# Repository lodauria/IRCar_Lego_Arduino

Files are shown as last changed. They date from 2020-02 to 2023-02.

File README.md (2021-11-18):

# Lego car controlled with IR
As optional project for the Reti Logiche course me and [Giorgia Benci](https://www.linkedin.com/in/giorgia-benci-1a4912186/) have created with Legos a remote controlled car that uses an Arduino Uno on board to control the electronic components, in particular a DC motor, a servomotor and a IR receiver. The remote control is performed using a Wii Nunchuk connected to an Arduino Uno that communicates with the car through an infrared LED. The main feature is that to control the car it can be used ether the joystick or the accelerometers of the Wii Nunchuk. 

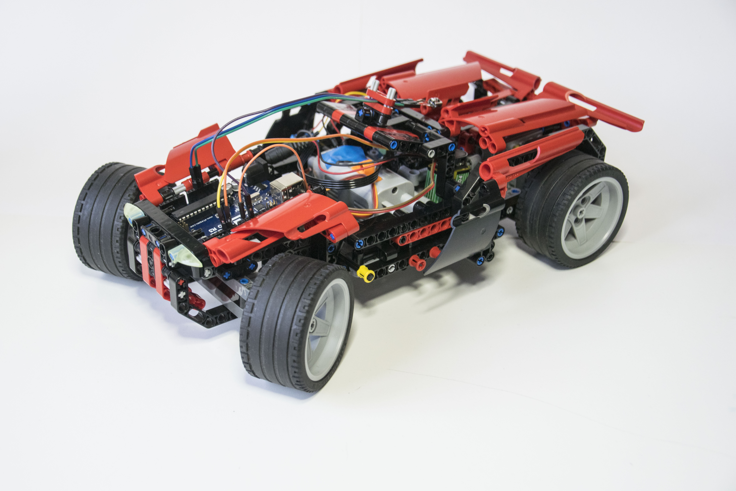
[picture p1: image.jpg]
Lego car


The Lego instructions are available [here](./LDD_files/Instructions), while the Lego Digital Designer 3D models can be found [here](./LDD_files/Models). The Arduino software developed is organized in the dedicated folders: [remote](./IRremote), [car](/IRlegocar).

***For Italian users*:** the complete documentation can be found [here](./Documentation.pdf).

## Demo video

To see the prototype in action and for more details about the system configuration watch the [video tutorial](https://youtu.be/qfQm9lA7alI).

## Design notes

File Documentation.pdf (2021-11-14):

# Macchina LEGO comandata a distanza

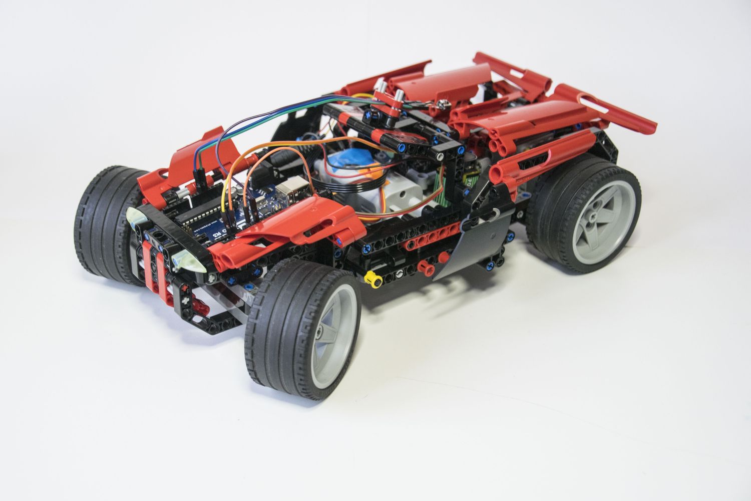
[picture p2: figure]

A cura di D’Auria Lorenzo e Benci Giorgia

## Introduzione

Il progetto in questione consiste nel comandare a distanza un’automobile costruita con i pezzi LEGO facendo uso del Nunchuk (controller di movimento) della Nintendo. Ciò avviene tramite la comunicazione infrarossi tra l’Arduino collegato al Nunchuk e l’Arduino integrato nella macchina LEGO. Come supporto alle componenti elettroniche, la scelta è ricaduta sui pezzi LEGO in quanto facilmente reperibili e maneggiabili.

## Descrizione della macchina

L’automobile è stata progettata in modo tale da ospitare in maniera specifica l’elettronica utilizzata, sfruttando inoltre il motore DC e la batteria in dotazione con i kit della LEGO (video dettagliato sull’adattamento di queste componenti). (https://youtu.be/au9P1RdKljY) Viene utilizzato un servo motore (anche esso adattato ai pezzi lego) (https://youtu.be/GeBPa39FLWI) per far sterzare le ruote anteriori, mentre il motore DC provvede da solo alla trazione attraverso le ruote posteriori. Per ottimizzarne le prestazioni del motore LEGO è stato necessario modificare la velocità di rotazione delle ruote attraverso una specifica combinazione di ingranaggi. Con l’ausilio del programma LEGO Digital Designer sono state generate le istruzioni dettagliate per la ricostruzione di questo modello (Istruzioni in PDF e modello 3D). (https://1drv.ms/f/s!AjiY4rjAO0lFgdFoaBNETIV-_LNzZQ)

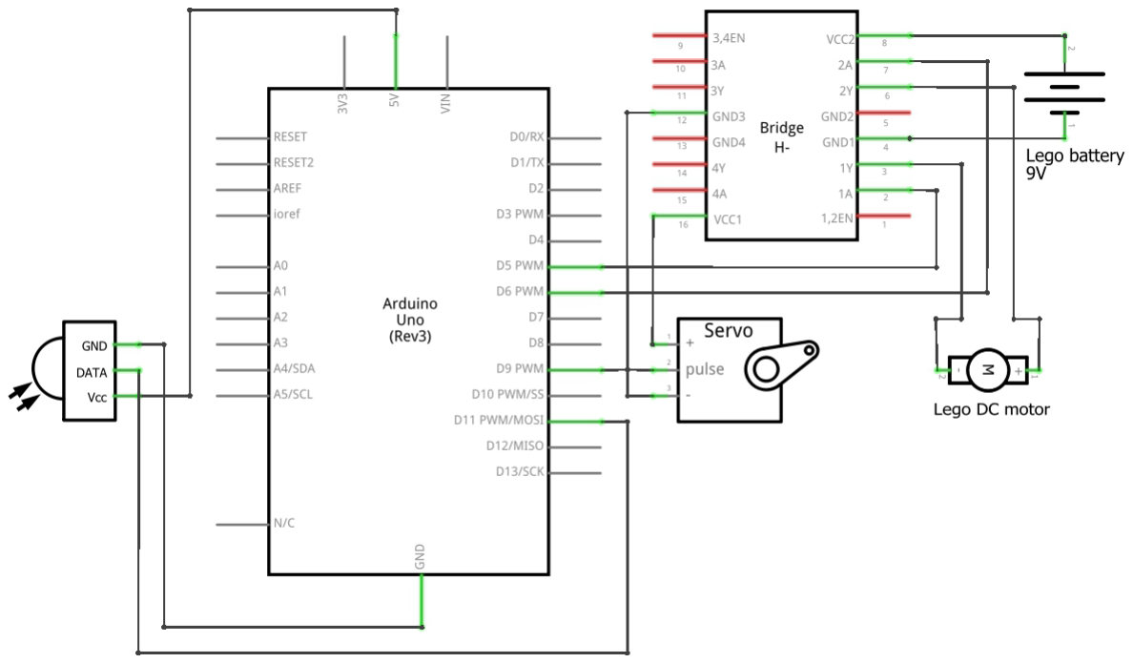
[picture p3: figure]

Schema dei componenti elettrici sull’auto
In linea di principio una volta che il sensore IR riceve un segnale, esso viene controllato per accertarsi che provenga dal telecomando e non sia dovuto ad interferenze, poi viene interpretato dall’Arduino presente sulla macchina, il quale comunica a sua volta al servo motore e all’H bridge le informazioni sul movimento dei motori. Va anche ricordato che all’interno del codice è stato inserito un “timer” che blocca la macchina in sicurezza in caso di mancanza del segnale per più di mezzo secondo (maggiori dettagli: codice IRlegocar.ino). (https://1drv.ms/u/s!AjiY4rjAO0lFgdFskilCLgVu3oVq1Q)
Una componente importante di questo sistema è l’H-Bridge, esso fornisce l’alimentazione di 5V al servo motore riducendo i 9V della batteria in dotazione, inoltre permette di comandare il motore DC (alimentato con 9V) in un senso o nell’altro utilizzando i segnali a basso voltaggio forniti dall’Arduino.
L’Arduino, e quindi il sensore IR a lui collegato, è alimentato separatamente da una batteria da 9V così da poter funzionare senza subire gli sbalzi di tensione dovuti al cambiamento della corrente nei motori.

## Controllo mediante Joystick

Per semplificare il funzionamento alla base del telecomando, è stato utilizzato inizialmente un semplice joystick compatibile con l’interfaccia Arduino con l’ausilio di una libreria apposita.

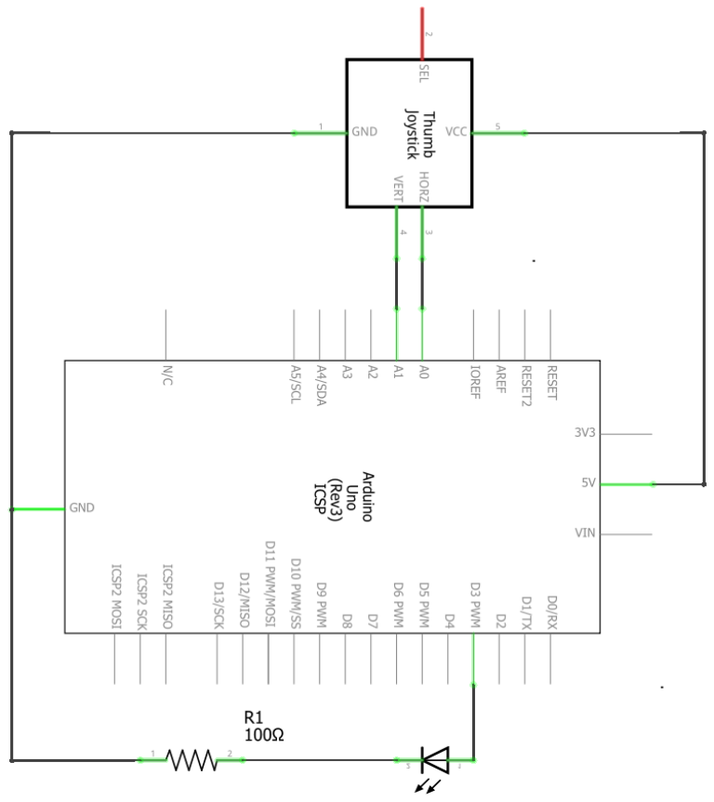
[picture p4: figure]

Schema elettrico del collegamento tra Arduino e il Joystick
In primo luogo, sono state effettuate delle misurazioni per individuare i valori di riferimento per ogni posizione del joystick, fondamentali per la calibrazione. Tali parametri vengono inseriti in delle funzioni lineari che calcolano i valori responsabili della gestione dei motori in base alla posizione del joystick.

In particolare, va e vb si riferiscono al voltaggio dei due morsetti del motore DC, mentre pos indica la posizione del servo motore. Tali dati vengono prima controllati ed eventualmente corretti (per eliminare valori non conformi), poi vengono inviati all’automobile (maggiori informazioni: codice IRjoystick.ino). (https://1drv.ms/u/s!AjiY4rjAO0lFgdJJfKvmslnTaNIrvg) Per fare ciò viene creata una sequenza di 12 bit (3 cifre esadecimali) costruita come illustrato sotto.

Var. | pos | va | vb
Bit # | 0 | 1 | 2 | 3 | 4 | 5 | 6 | 7 | 8 | 9 | 10 | 11

Tale stringa viene inviata tramite il LED IR secondo lo standard Sony che prevede l’utilizzo di un segnale con una frequenza di 38kHz contenente 12 bit di dati [1]
. Sperimentalmente si è verificato che il protocollo scelto è il più performante per la coppia LED-sensore a disposizione.

## Controllo mediante Nunchuk

Per aumentare la complessità del sistema di controllo, si è passati all’utilizzo del Nunchuk, l’accessorio della Nintendo per la console Nintendo Wii; esso è dotato di un accelerometro, un joystick e di due pulsanti sul retro (C e Z) e non possiede un sistema di alimentazione proprio.
Il Nunchuk lavora con una tensione di 3.3V e fornisce due uscite analogiche; i dati in uscita dal Nunchuk vengono trasmessi mediante il sistema di comunicazione seriale I²
C, il quale risulta vantaggioso per comunicare numerosi dati con l’impiego di solamente due linee (Serial Data e Serial

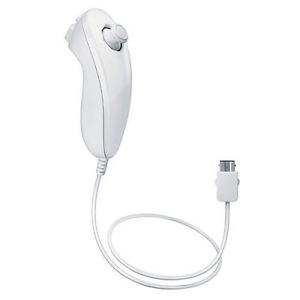
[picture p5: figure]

Clock). Il Nunchuk trasmette sulla SDA 6 bytes, come descritto nella seguente tabella [2] :
Bytes inviati | Indirizzo
Asse x del joystick | 0x00
Asse y del joystick | 0x01
Asse x dell’accelerometro (bit da 9 a 2) | 0x02
Asse y dell’accelerometro (bit da 9 a 2) | 0x03
Asse z dell’accelerometro (bit da 9 a 2) | 0x04
Accel. Z Bit 1 | Accel. Z Bit 0 | Accel. Y Bit 1 | Accel. Y Bit 0 | Accel. X Bit 1 | Accel. X Bit 0 | Bottone C | Bottone Z | 0x05

Per interfacciare il Nunchuk al microcontrollore Arduino si procede come in figura.

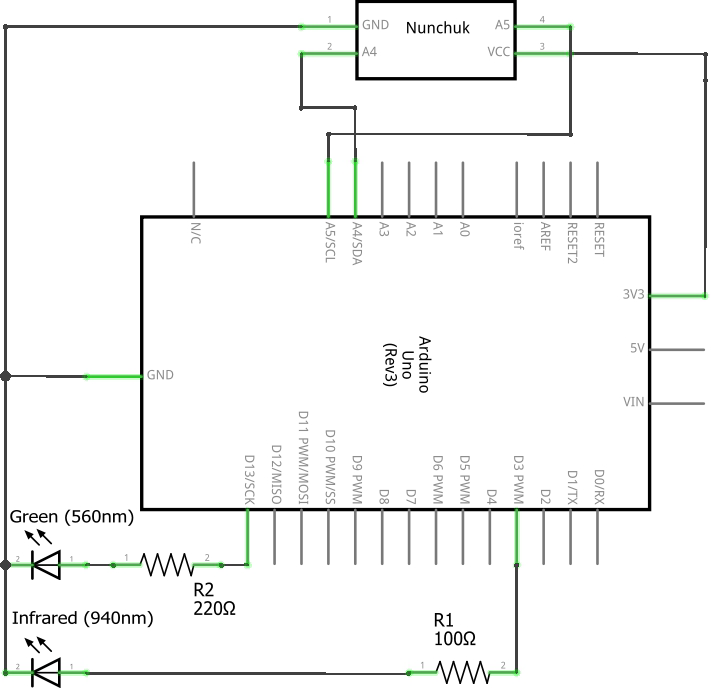
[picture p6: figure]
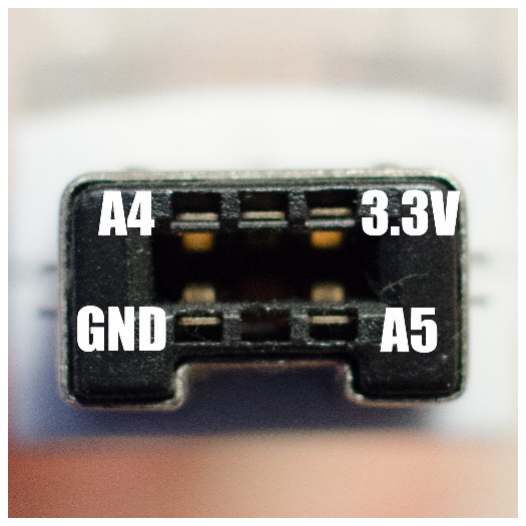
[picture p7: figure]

Grazie alla libreria ArduinoNunchuk.h [3] da includere nel codice, si estraggono con facilità tutti gli stati del joystick, dell’accelerometro e dei bottoni. In questo caso si è voluto sfruttare la doppia funzionalità del Nunchuk in modo tale da poter controllare l’automobile in due modalità diverse (per cambiare modalità basta premere il tasto Z):
1) Con il joystick | (Led verde spento)
2) Con l’accelerometro | (Led verde acceso)
Una volta rilevati i dati provenienti dal Nunchuk, si procede in maniera del tutto analoga al caso del joystick appena visto, ovvero si genera e si invia una sequenza di 12 bit dello stesso tipo (maggiori informazioni: codice IRremote.ino). (https://1drv.ms/u/s!AjiY4rjAO0lFgdF19pDOsytSu_w8uw)

Connettore del Nunchuk

## Considerazioni e commenti finali

Per concludere, sebbene certi dettagli nella progettazione possano risultare non ottimizzati al meglio, la resa finale è stata più che soddisfacente.
Ecco alcuni aspetti che potrebbero essere migliorati:
- Inevitabilmente un valore tra va e vb sarà nullo, quindi l’utilizzo di 12 bit può risultare uno spreco. Con 12 bit, poiché il dato pos ne richiede già 4, si potevano gestire 256 velocità al posto di 31. Soluzione ancora più intelligente sarebbe stata usare 6 bit per 64 gradazioni di velocità (che sono più che sufficienti) e lasciare 2 ulteriori bit per un codice di verifica che aumenterebbe l’affidabilità del controllo sui dati ricevuti.
- La luce prodotta dal LED IR utilizzato è molto meno intensa rispetto a quella prodotta da un telecomando tradizionale. Sebbene la resistenza di 100 Ω utilizzata sia la minima possibile, la

portata del segnale non supera il metro e mezzo. Ovviamente l’utilizzo di un LED più performante o di un ricevitore più sensibile sarebbe fondamentale per aumentare la portata del segnale.
- L’utilizzo di una sola batteria sulla macchina sarebbe più conveniente ed elegante, a patto che si risolva il problema del calo di tensione nell’Arduino quando entrambi i motori sono alimentati al massimo.
- Le ruote sterzanti si muovono in 16 diverse gradazioni (valori di pos da 0 a 15), quindi, poiché si è posto il valore centrale (ruote dritte) a pos=8, ci sono 7 gradazioni di sterzo a destra e 8 a sinistra. Sarebbe ottimale riuscire ad avere un numero di gradazioni di sterzo dispari così da poter avere gli stessi angoli di sterzo a destra e a sinistra.
Online è presente un video che mostra in maniera più dettagliata gli accorgimenti tecnici che sono stati utilizzati per realizzare questo progetto (link), (https://youtu.be/qfQm9lA7alI) mentre i dettagli riguardo all’implementazione dei codici si trovano all’interno degli stessi come commento.

Programmi: Arduino Genuino, Fritzing.
Fonti:
[1] http://www.mauroalfieri.it/elettronica/tutorial-arduino-come-trasmettitore-ir-o-come-telecomando.html (http://www.mauroalfieri.it/elettronica/tutorial-arduino-come-trasmettitore-ir-o-come-telecomando.html) Tutorial sulla comunicazione infrarossi.
[2] https://bootlin.com/labs/doc/nunchuk.pdf Descrizione della comunicazione seriale del Nunchuk con l’esterno + traduzione dello schema.
[3] http://www.marcopucci.it/tutorial-arduino-7-wii-nunchuck-e-motorini-servo/ Tutorial sull’utilizzo del Nunchuk.

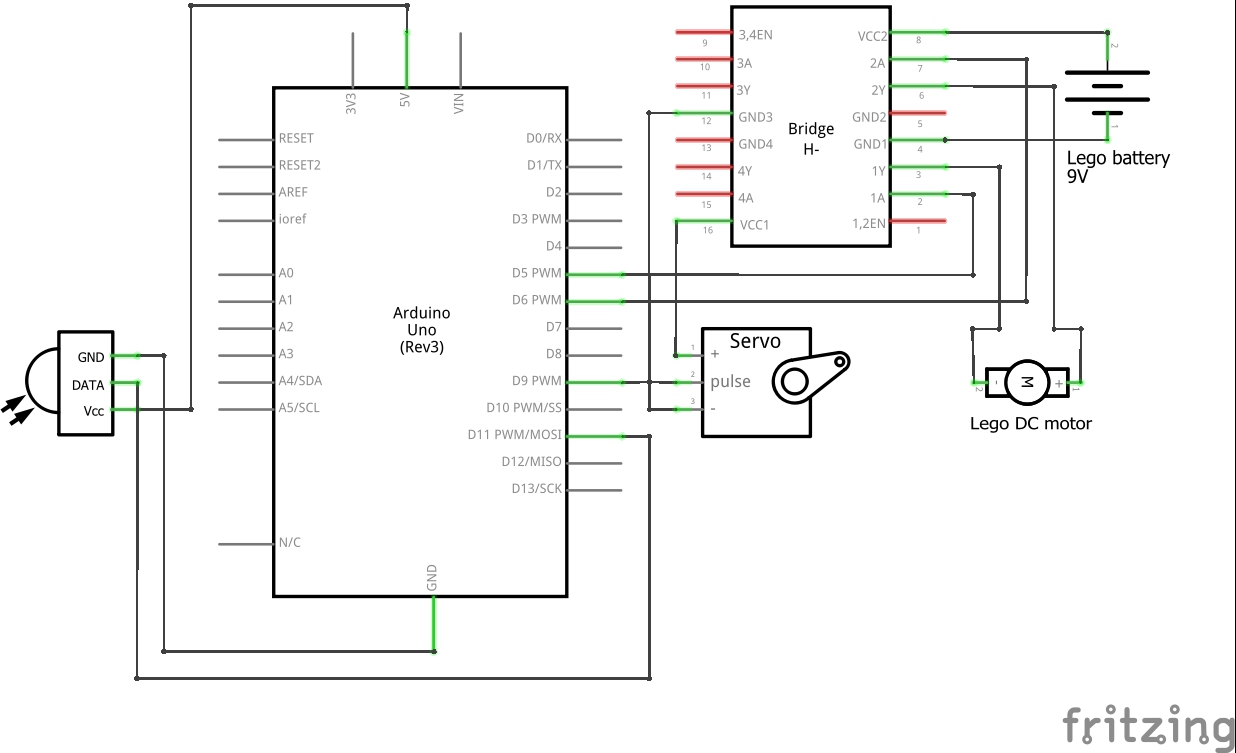
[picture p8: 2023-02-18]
IRlegocar/Schema macchina.jpg

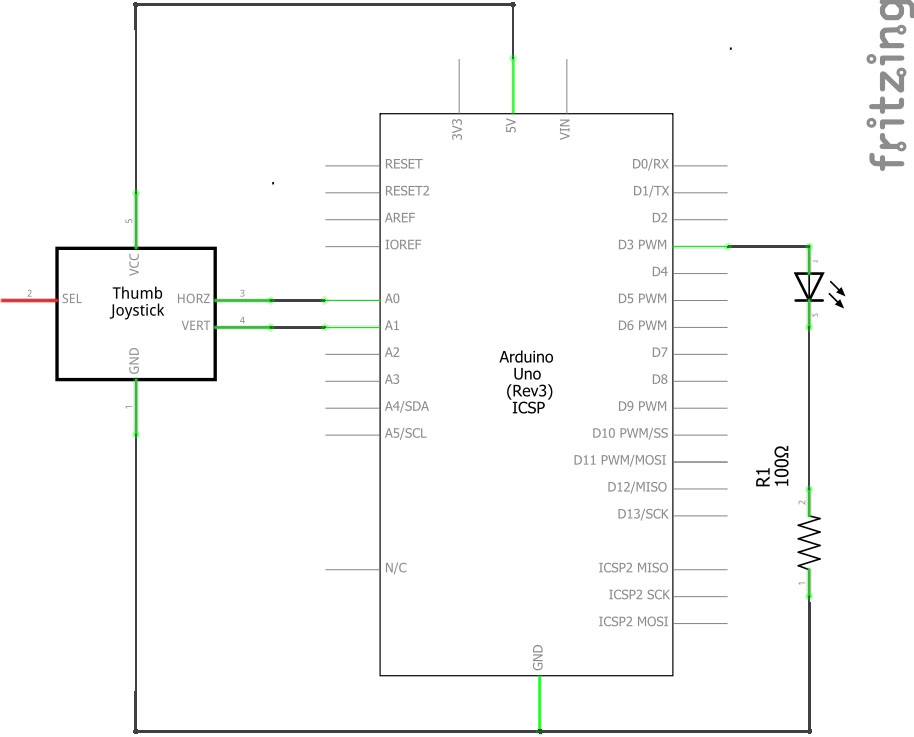
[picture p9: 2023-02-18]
IRjoystick/Schema joystick.jpg

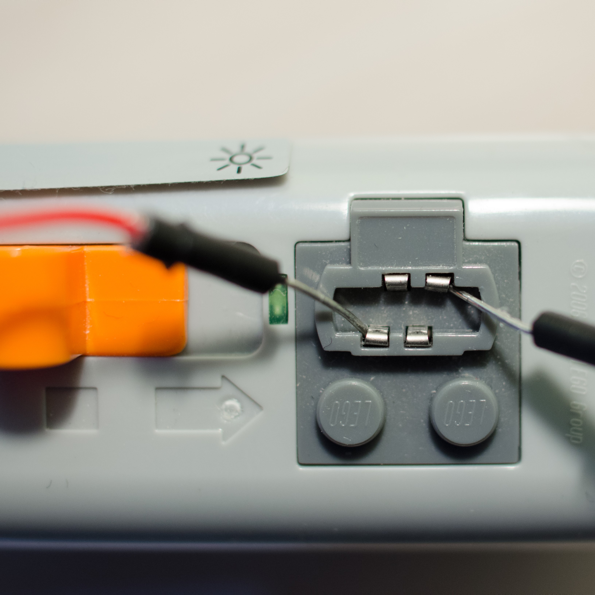
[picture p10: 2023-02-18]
IRlegocar/Collegamento batteria.JPG

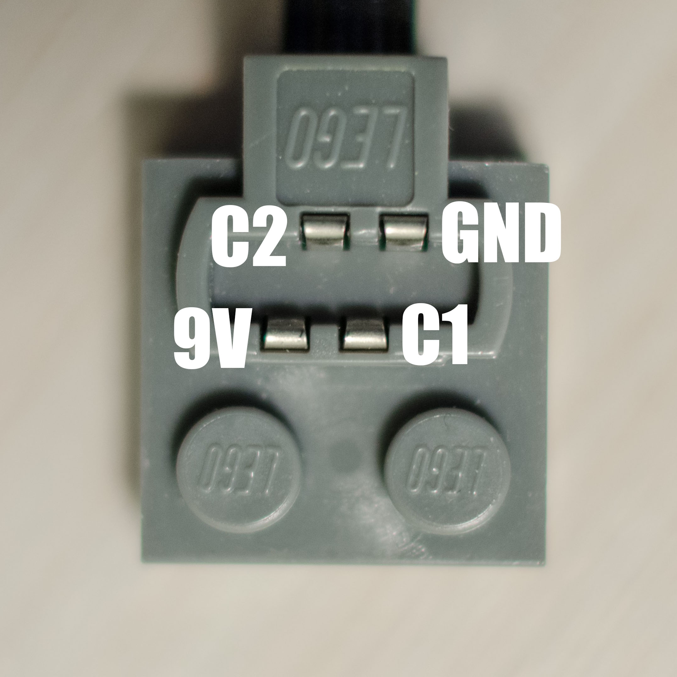
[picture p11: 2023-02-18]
IRlegocar/Lego socket.jpg

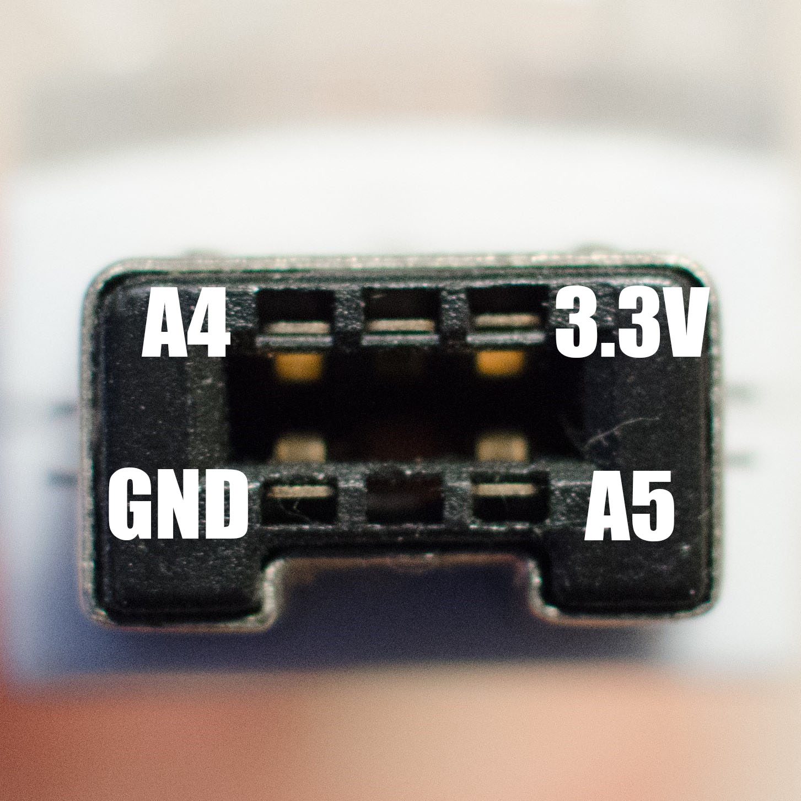
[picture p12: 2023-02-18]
IRremote/Nunchuk socket.jpg

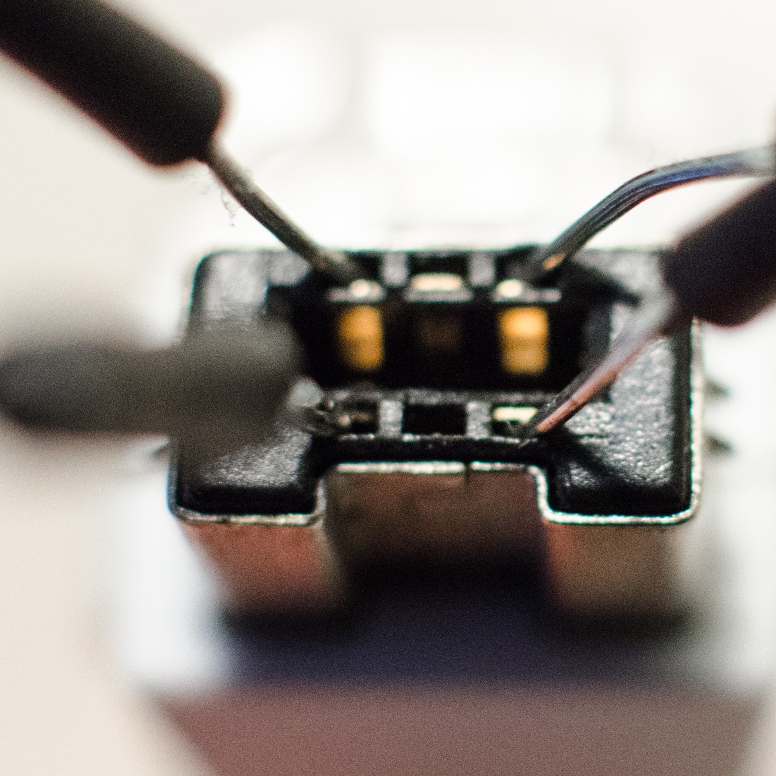
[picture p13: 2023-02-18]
IRremote/Collegamento nunchuk.JPG

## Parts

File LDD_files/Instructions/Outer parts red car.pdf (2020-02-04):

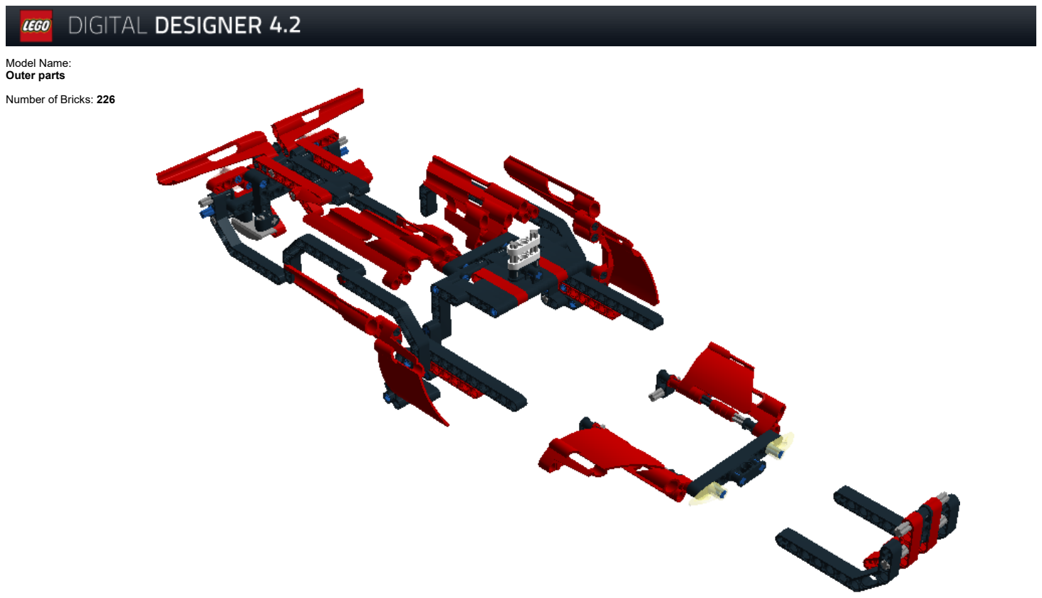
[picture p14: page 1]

Model Name:
Outer parts

Number of Bricks: 226

1 x

1 x

1 x

Step 1 of 90

1 x

1 x

1 x

1 x

Step 2 of 90

Step 3 of 90

1 x

1 x

Step 4 of 90

2 x

Step 5 of 90

1 x

1 x

1 x

1 x

Step 6 of 90

Step 7 of 90

1 x

Step 8 of 90

1 x

1 x

1 x

1 x

Step 9 of 90

1 x

1 x

1 x

1 x

Step 10 of 90

1 x

Step 11 of 90

1 x

1 x

Step 12 of 90

2 x

Step 13 of 90

Step 14 of 90

1 x

1 x

Step 15 of 90

1 x

Step 16 of 90

1 x

1 x

Step 17 of 90

Step 18 of 90

1 x

1 x

Step 19 of 90

Step 20 of 90

2 x

1 x

Step 21 of 90

Step 22 of 90

Step 23 of 90

1 x

1 x

Step 24 of 90

2 x

2 x

Step 25 of 90

1 x

3 x

Step 26 of 90

1 x

1 x

1 x

1 x

Step 27 of 90

1 x

1 x

1 x

1 x

Step 28 of 90

1 x

1 x

2 x

Step 29 of 90

2 x

1 x

1 x

Step 30 of 90

1 x

1 x

Step 31 of 90

1 x

1 x

Step 32 of 90

1 x

1 x

1 x

Step 33 of 90

Step 34 of 90

1 x

Step 35 of 90

1 x

1 x

1 x

1 x

Step 36 of 90

2 x

1 x

1 x

Step 37 of 90

1 x

1 x

2 x

Step 38 of 90

2 x

Step 39 of 90

1 x

1 x

Step 40 of 90

1 x

1 x

1 x

1 x

Step 41 of 90

1 x

1 x

1 x

1 x

Step 42 of 90

1 x

2 x

1 x

Step 43 of 90

2 x

1 x

1 x

Step 44 of 90

1 x

1 x

1 x

1 x

Step 45 of 90

1 x

1 x

1 x

Step 46 of 90

1 x

2 x

1 x

Step 47 of 90

Step 48 of 90

1 x

Step 49 of 90

1 x

1 x

2 x

Step 50 of 90

1 x

1 x

1 x

1 x

Step 51 of 90

1 x

1 x

1 x

1 x

Step 52 of 90

1 x

1 x

Step 53 of 90

3 x

1 x

Step 54 of 90

1 x

1 x

1 x

1 x

Step 55 of 90

1 x

1 x

Step 56 of 90

1 x

2 x

1 x

Step 57 of 90

Step 58 of 90

Step 59 of 90

1 x

1 x

Step 60 of 90

1 x

1 x

1 x

1 x

Step 61 of 90

2 x

1 x

1 x

Step 62 of 90

1 x

1 x

1 x

1 x

Step 63 of 90

1 x

1 x

1 x

1 x

Step 64 of 90

2 x

1 x

1 x

Step 65 of 90

1 x

1 x

2 x

Step 66 of 90

1 x

1 x

1 x

1 x

Step 67 of 90

1 x

Step 68 of 90

1 x

Step 69 of 90

1 x

1 x

1 x

1 x

Step 70 of 90

1 x

Step 71 of 90

2 x

Step 72 of 90

1 x

1 x

2 x

Step 73 of 90

1 x

Step 74 of 90

1 x

2 x

1 x

Step 75 of 90

1 x

1 x

Step 76 of 90

Step 77 of 90

1 x

2 x

1 x

Step 78 of 90

1 x

1 x

Step 79 of 90

Step 80 of 90

1 x

1 x

Step 81 of 90

1 x

1 x

1 x

1 x

Step 82 of 90

1 x

2 x

1 x

Step 83 of 90

1 x

1 x

1 x

1 x

Step 84 of 90

1 x

1 x

2 x

Step 85 of 90

1 x

1 x

Step 86 of 90

2 x

2 x

Step 87 of 90

1 x

Step 88 of 90

Step 89 of 90

Step 90 of 90

5 x | 4142822 TECHNIC 3M BEAM - Black | 6 x | 4140429 TECHNIC 5M BEAM - Black | 2 x | 4128589 TECHNIC 5M BEAM - Bright Red
3 x | 3252426 TECHNIC 7M BEAM - Black | 2 x | 4162098 TECHNIC 7M BEAM - Bright
Red | 6 x | 4120017 TECHNIC ANG. BEAM 4X2
90 DEG - Black
2 x | 4125200 TECHNIC ANG. BEAM 4X2
90 DEG - Bright Red | 1 x | 4154767 TECHNIC 9M BEAM - Black | 2 x | 4192225 TECHNIC 9M BEAM - Bright Red
3 x | 4156150 TECHNIC 11M BEAM -
Black | 2 x | 4142823 TECHNIC ANG. BEAM 3X5
90 DEG. - Black | 4 x | 3234821 TECHNIC ANGULAR BEAM
4X4 - Bright Red
8 x | 4107578 DOUBLE ANGULAR BEAM
3X7 45° - Black | 4 x | 4186678 TECHNIC LEVER 2M -
Bright Red | 2 x | 663201 TECHNIC LEVER 3M - White
4 x | 4142236 LEVER 1X4, WITHOUT
NOTCH - Black | 4 x | 4142865 2M CROSS AXLE W.
GROOVE - Bright Red | 30 x | 278026 CONNECTOR PEG W.
FRICTION - Black
1 x | 4211807 CONNECTOR PEG -
Medium Stone Grey
13 x | 4211815 CROSS AXLE 3M -
Medium Stone Grey
7 x | 4177421 BUSH FOR CROSS AXLE -
Black

2 x | 4227155 BUSH FOR CROSS AXLE -
Bright Red | 27 x | 4189110

CONN.BUSH
W.FRIC./CROSSALE -
Bright Blue
1 x | 370526 CROSS AXLE 4M - Black
2 x | 4125189 CROSS AXLE, EXTENSION
M/3 RIBS - Bright Red | 21 x | 4514553 CONNECTOR PEG W.
FRICTION 3M - Bright Blue | 1 x | 4211709 3M CONNECTOR PEG -
Medium Stone Grey
2 x | 4107081 CATCH W. CROSS HOLE -
Black | 5 x | 4211639 CROSS AXLE 5M - Medium
Stone Grey | 8 x | 653626 CROSS BLOCK 90° - Black
2 x | 4119033 ANGLE ELEMENT, 0
DEGREES [1] - Bright Red | 2 x | 4515185 BEAM 1X2 W/CROSS AND
HOLE - Black | 2 x | 370626 CROSS AXLE 6M - Black
2 x | 4107742 2M FRIC. SNAP W/CROSS
HOLE - Black | 2 x | 4211805 CROSS AXLE 7M - Medium
Stone Grey | 5 x | 4121667 DOUBLE CROSS BLOCK -
Black
4 x | 4107783 ANGLE ELEMENT, 180
DEGREES [2] - Black | 1 x | 4140430 TECHNIC CROSS BLOCK
2X1 - Black | 2 x | 4143466 TECHNIC CROSSBLOCK
2X3 - Black

2 x | 4185661 BION. EYE - Bright Red | 4 x | 4163567 BION. EYE - Tr. Red | 2 x | 4163577 BION. EYE - Tr. Fluore. Green
2 x | 4153010

SIDE SKIRTS 1X4X1
W/DOUBL/SNAP - Medium
Stone Grey
2 x | 4143152 RIGHT 3D-PANEL 5M-5 -
Bright Red | 2 x | 4143150 LEFT 3D-PANEL 5M-6 - Bright Red
2 x | 4158891 RIGHT 3D-PANEL 10M-7 -
Bright Red | 2 x | 4158886 LEFT 3D-PANEL 10M-8 -
Bright Red | 2 x | 4205040 RIGHT 3D PANEL 7M W
Ø4.85 NO22 - Bright Red
2 x | 4205041 LEFT 3D PANEL 7M W
Ø4.85 NO23 - Bright Red | 1 x | 4125179 RIGHT 3D PANEL 12M-3 -
Bright Red | 1 x | 4125180 LEFT 3D PANEL 12M-4 -
Bright Red

© 2012 The LEGO Group. All rights reserved. Use of the LEGO Digital Designer html print tool, signifies your agreement to the terms of use.

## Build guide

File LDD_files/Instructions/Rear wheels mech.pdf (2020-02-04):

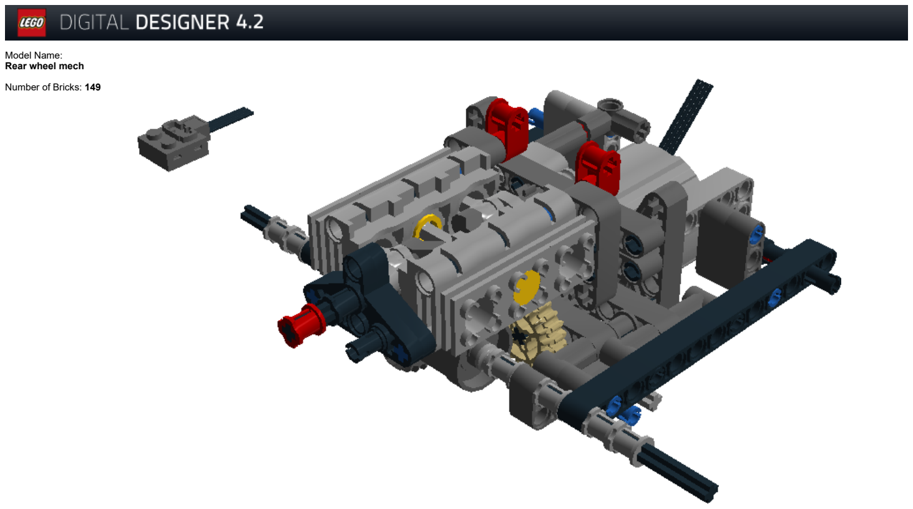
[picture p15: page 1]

Model Name:
Rear wheel mech

Number of Bricks: 149

1 x

Step 1 of 67

1 x

1 x

1 x

Step 2 of 67

1 x

1 x

Step 3 of 67

2 x

Step 4 of 67

2 x

1 x

Step 5 of 67

Step 6 of 67

1 x

Step 7 of 67

1 x

1 x

1 x

1 x

Step 8 of 67

1 x

Step 9 of 67

1 x

1 x

Step 10 of 67

1 x

Step 11 of 67

2 x

2 x

Step 12 of 67

1 x

3 x

Step 13 of 67

1 x

1 x

1 x

Step 14 of 67

1 x

Step 15 of 67

1 x

1 x

1 x

1 x

Step 16 of 67

1 x

1 x

Step 17 of 67

Step 18 of 67

1 x

1 x

1 x

Step 19 of 67

2 x

1 x

Step 20 of 67

1 x

Step 21 of 67

2 x

2 x

Step 22 of 67

Step 23 of 67

1 x

2 x

Step 24 of 67

Step 25 of 67

1 x

1 x

1 x

Step 26 of 67

2 x

1 x

1 x

Step 27 of 67

1 x

1 x

1 x

Step 28 of 67

1 x

1 x

1 x

Step 29 of 67

2 x

1 x

Step 30 of 67

Step 31 of 67

1 x

1 x

2 x

Step 32 of 67

1 x

2 x

1 x

Step 33 of 67

2 x

1 x

1 x

Step 34 of 67

2 x

2 x

Step 35 of 67

1 x

Step 36 of 67

2 x

1 x

Step 37 of 67

Step 38 of 67

1 x

1 x

Step 39 of 67

1 x

Step 40 of 67

1 x

Step 41 of 67

3 x

1 x

Step 42 of 67

Step 43 of 67

1 x

Step 44 of 67

1 x

1 x

1 x

1 x

Step 45 of 67

2 x

1 x

1 x

Step 46 of 67

1 x

Step 47 of 67

1 x

1 x

1 x

Step 48 of 67

1 x

2 x

1 x

Step 49 of 67

1 x

2 x

1 x

Step 50 of 67

1 x

1 x

1 x

Step 51 of 67

1 x

Step 52 of 67

1 x

1 x

Step 53 of 67

1 x

1 x

1 x

1 x

Step 54 of 67

2 x

1 x

1 x

Step 55 of 67

1 x

Step 56 of 67

1 x

Step 57 of 67

2 x

2 x

Step 58 of 67

Step 59 of 67

2 x

Step 60 of 67

1 x

1 x

1 x

1 x

Step 61 of 67

2 x

1 x

Step 62 of 67

Step 63 of 67

1 x

Step 64 of 67

1 x

1 x

1 x

1 x

Step 65 of 67

Step 66 of 67

Step 67 of 67

3 x | 4506081

FUNC. MOTOR Ø40X6M -
Black,Bright
Orange,Medium Stone
Grey,Dark Stone Grey
2 x | 4210751 TECHNIC 3M BEAM - Dark
Stone Grey | 4 x | 4210667 TECHNIC ANG. BEAM 4X2 90 DEG - Dark Stone Grey
3 x | 4210757 TECHNIC 9M BEAM - Dark
Stone Grey | 1 x | 4210755 TECHNIC 11M BEAM - Dark
Stone Grey | 2 x | 4164422 TECHNIC 13M BEAM -
Black
2 x | 4210753 TECHNIC ANG. BEAM 3X5
90 DEG. - Dark Stone Grey | 4 x | 4211713

TECHNIC ANG. BEAM 3X5
90 DEG. - Medium Stone
Grey
2 x | 290526 TRIANGLE - Black
4 x | 4210689 TRIANGLE - Dark Stone
Grey | 3 x | 4211573 1/2 BUSH - Medium Stone
Grey | 4 x | 4142865 2M CROSS AXLE W.
GROOVE - Bright Red
24 x | 278026 CONNECTOR PEG W.
FRICTION - Black | 5 x | 4211815 CROSS AXLE 3M - Medium
Stone Grey | 2 x | 4186017 CONNECTOR PEG/CROSS
AXLE - Brick Yellow
1 x | 4177421 BUSH FOR CROSS AXLE -
Black | 7 x | 4211622 BUSH FOR CROSS AXLE -
Medium Stone Grey | 1 x | 4227155 BUSH FOR CROSS AXLE -
Bright Red
10 x | 4189110 CONN.BUSH
W.FRIC./CROSSALE -
Bright Blue
2 x | 370526 CROSS AXLE 4M - Black | 6 x | 4112203 PLASTIC MOTOR, PISTON
- Bright Yellow

11 x | 4514553 CONNECTOR PEG W.
FRICTION 3M - Bright Blue | 1 x | 4516546

CROSS AXLE,
EXTENSION, 2M - Dark
Stone Grey
2 x | 4210987 PLASTIC MOTOR, CRANK
- Dark Stone Grey
1 x | 4114740 CROSS AXLE 5M - Black | 3 x | 4210851 CROSS BLOCK 90° - Dark
Stone Grey | 2 x | 4118881 CROSS BLOCK 90° - Bright
Red
3 x | 4210658

ANGLE ELEMENT, 0
DEGREES [1] - Dark Stone
Grey
1 x | 4515184 BEAM 1X2 W/CROSS AND
HOLE - Medium Stone Grey | 6 x | 4211379 PLASTIC MOTOR, MAIN ROD - Medium Stone Grey
2 x | 4211609

PLASTIC MOTOR,
CRANK/CROSS - Medium
Stone Grey
4 x | 4107742 2M FRIC. SNAP W/CROSS
HOLE - Black | 1 x | 4121667 DOUBLE CROSS BLOCK - Black
1 x | 4210857 CROSS BLOCK 3M - Dark
Stone Grey | 2 x | 373726 CROSS AXLE 10M - Black | 1 x | 4210671

ANGLE ELEMENT, 90
DEGREES [6] - Dark Stone
Grey
1 x | 4225033 BEAM 3 M. W/4 SNAPS -
Medium Stone Grey | 6 x | 4234251

PLASTIC MOTOR,
CYLINDER - Medium Stone
Grey
1 x | 4296059 Angular beam 90degr. w.4
snaps - Medium Stone Grey

3 x | 4140445 CONICAL WHEEL Z12 -
Brick Yellow | 3 x | 4514559 GEAR WHEEL T=8, M=1 -
Dark Stone Grey | 1 x | 4177431 DOUBLE CONICAL WHEEL
Z12 1M - Black
1 x | 4514555 DOUBLE CONICAL WHEEL
Z20 1M - Brick Yellow | 1 x | 4514558 GEAR WHEEL Z24 - Dark
Stone Grey | 1 x | 4525184 DIFFERENTIALE 3M Z 28 -
Dark Stone Grey

© 2012 The LEGO Group. All rights reserved. Use of the LEGO Digital Designer html print tool, signifies your agreement to the terms of use.

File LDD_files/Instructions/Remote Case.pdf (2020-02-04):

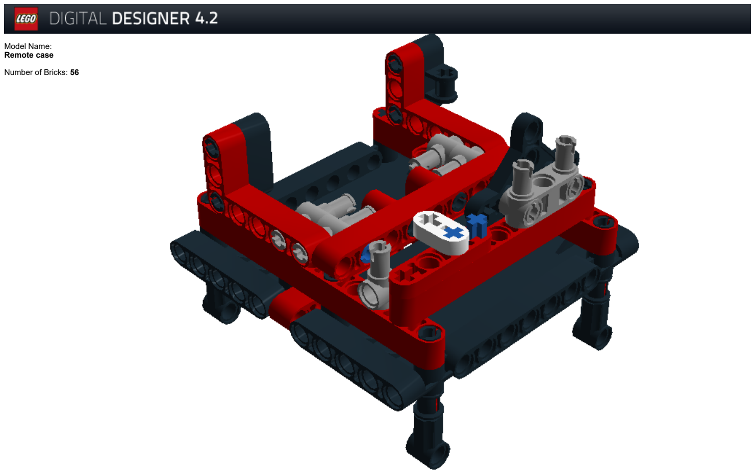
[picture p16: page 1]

Model Name:
Remote case

Number of Bricks: 56

1 x

Step 1 of 26

1 x

3 x

Step 2 of 26

1 x

3 x

Step 3 of 26

1 x

1 x

2 x

Step 4 of 26

1 x

2 x

1 x

Step 5 of 26

2 x

2 x

Step 6 of 26

1 x

1 x

Step 7 of 26

1 x

1 x

1 x

Step 8 of 26

Step 9 of 26

1 x

2 x

Step 10 of 26

1 x

1 x

Step 11 of 26

Step 12 of 26

1 x

1 x

1 x

Step 13 of 26

Step 14 of 26

1 x

1 x

1 x

Step 15 of 26

Step 16 of 26

1 x

1 x

1 x

Step 17 of 26

Step 18 of 26

1 x

2 x

1 x

Step 19 of 26

Step 20 of 26

1 x

1 x

Step 21 of 26

1 x

1 x

2 x

Step 22 of 26

Step 23 of 26

1 x

1 x

2 x

Step 24 of 26

1 x

1 x

Step 25 of 26

Step 26 of 26

1 x | 4142822 TECHNIC 3M BEAM - Black | 1 x | 4162098 TECHNIC 7M BEAM - Bright
Red | 1 x | 4125200 TECHNIC ANG. BEAM 4X2
90 DEG - Bright Red
2 x | 4192225 TECHNIC 9M BEAM - Bright
Red | 1 x | 4205035 TECHNIC 11M BEAM -
Bright Red | 4 x | 4143154 TECHNIC ANG. BEAM 3X5
90 DEG. - Bright Red
1 x | 4163533 TECHNIC LEVER 2M -
White | 1 x | 4141811

LEVER 1X4, WITHOUT
NOTCH - Bright Red | 1 x | 6010864 TRIANGEL - Black
2 x | 4211483 CONNECTOR PEG W.
KNOB - Medium Stone Grey | 3 x | 4142865 2M CROSS AXLE W.
GROOVE - Bright Red | 16 x | 278026 CONNECTOR PEG W.
FRICTION - Black
2 x | 4225927 CONNECTOR PEG/CROSS
AXLE - Bright Blue | 1 x | 4227155 BUSH FOR CROSS AXLE -
Bright Red | 1 x | 370526 CROSS AXLE 4M - Black
2 x | 4514553 CONNECTOR PEG W.
FRICTION 3M - Bright Blue | 4 x | 4107085 ANGLE ELEMENT, 0
DEGREES [1] - Black | 3 x | 4107742 2M FRIC. SNAP W/CROSS
HOLE - Black
5 x | 4560175 DOUBLE BUSH 3M Ø4.9 -
Medium Stone Grey
1 x | 6007966 CROSS BLOCK 3X2 - Black | 1 x | 4225033 BEAM 3 M. W/4 SNAPS - Medium Stone Grey

2 x | 4566243 FLAT PANEL - Black

© 2012 The LEGO Group. All rights reserved. Use of the LEGO Digital Designer html print tool, signifies your agreement to the terms of use.

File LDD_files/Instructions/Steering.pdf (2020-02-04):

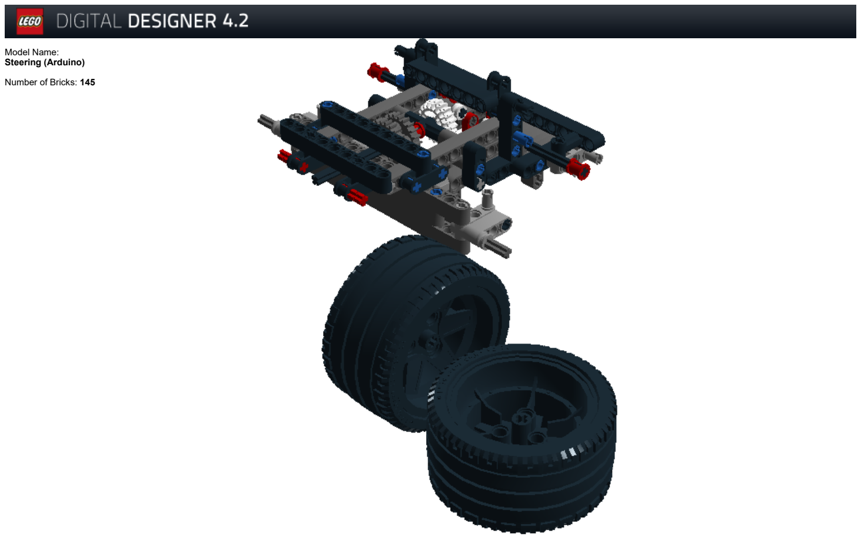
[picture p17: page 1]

Model Name:
Steering (Arduino)

Number of Bricks: 145

1 x

1 x

Step 1 of 67

Step 2 of 67

1 x

1 x

Step 3 of 67

Step 4 of 67

1 x

Step 5 of 67

1 x

2 x

1 x

Step 6 of 67

3 x

1 x

Step 7 of 67

1 x

1 x

1 x

1 x

Step 8 of 67

1 x

1 x

1 x

Step 9 of 67

1 x

1 x

1 x

1 x

Step 10 of 67

1 x

1 x

1 x

1 x

Step 11 of 67

1 x

Step 12 of 67

1 x

2 x

1 x

Step 13 of 67

Step 14 of 67

1 x

Step 15 of 67

1 x

1 x

Step 16 of 67

Step 17 of 67

1 x

Step 18 of 67

2 x

1 x

1 x

Step 19 of 67

1 x

1 x

1 x

Step 20 of 67

Step 21 of 67

1 x

1 x

Step 22 of 67

Step 23 of 67

1 x

1 x

Step 24 of 67

2 x

Step 25 of 67

1 x

1 x

Step 26 of 67

2 x

2 x

Step 27 of 67

3 x

1 x

Step 28 of 67

1 x

1 x

1 x

1 x

Step 29 of 67

1 x

2 x

1 x

Step 30 of 67

1 x

2 x

1 x

Step 31 of 67

Step 32 of 67

1 x

Step 33 of 67

1 x

Step 34 of 67

2 x

Step 35 of 67

1 x

1 x

Step 36 of 67

1 x

1 x

2 x

Step 37 of 67

1 x

Step 38 of 67

2 x

1 x

Step 39 of 67

Step 40 of 67

1 x

Step 41 of 67

1 x

1 x

1 x

1 x

Step 42 of 67

1 x

1 x

1 x

1 x

Step 43 of 67

1 x

1 x

Step 44 of 67

2 x

1 x

Step 45 of 67

Step 46 of 67

1 x

Step 47 of 67

1 x

Step 48 of 67

1 x

1 x

1 x

1 x

Step 49 of 67

1 x

2 x

1 x

Step 50 of 67

2 x

1 x

Step 51 of 67

Step 52 of 67

1 x

1 x

1 x

Step 53 of 67

1 x

1 x

1 x

1 x

Step 54 of 67

1 x

1 x

1 x

1 x

Step 55 of 67

1 x

2 x

1 x

Step 56 of 67

1 x

1 x

2 x

Step 57 of 67

1 x

Step 58 of 67

1 x

1 x

Step 59 of 67

Step 60 of 67

1 x

1 x

Step 61 of 67

Step 62 of 67

1 x

1 x

Step 63 of 67

1 x

1 x

1 x

Step 64 of 67

1 x

2 x

Step 65 of 67

Step 66 of 67

Step 67 of 67

1 x | 4210998 PLATE 1X8 - Dark Stone
Grey | 2 x | 4262086 RIM Ø 56 X 34 - Black | 2 x | 4192535 TYRE LOW WIDE Ø68,8 X 36 - Black
1 x | 4142822 TECHNIC 3M BEAM - Black | 2 x | 4211655 TECHNIC 3M BEAM -
Medium Stone Grey | 2 x | 4140429 TECHNIC 5M BEAM - Black
2 x | 4210686 TECHNIC 5M BEAM - Dark
Stone Grey | 1 x | 3252426 TECHNIC 7M BEAM - Black | 2 x | 4154767 TECHNIC 9M BEAM - Black
2 x | 4210757 TECHNIC 9M BEAM - Dark
Stone Grey | 3 x | 4210755 TECHNIC 11M BEAM - Dark
Stone Grey | 1 x | 4128603 TECHNIC 15M BEAM -
Black
3 x | 4210687 TECHNIC 15M BEAM -
Dark Stone Grey | 2 x | 4142823 TECHNIC ANG. BEAM 3X5
90 DEG. - Black | 4 x | 4210753 TECHNIC ANG. BEAM 3X5
90 DEG. - Dark Stone Grey
4 x | 663226 TECHNIC LEVER 3M - Black | 4 x | 4144138 LEVER 1X4, WITHOUT
NOTCH - White | 4 x | 4210659 TECHNIC LEVER 3X3M,
90° - Dark Stone Grey
2 x | 290521 TRIANGLE - Bright Red | 2 x | 4211573 1/2 BUSH - Medium Stone Grey
2 x | 4193512 1/2 BUSH - White

6 x | 4143005 CONNECTOR PEG W.
KNOB - Bright Blue | 2 x | 4142865 2M CROSS AXLE W.
GROOVE - Bright Red | 4 x | 4211050 1 1/2 M CONNECTING
BUSH - Dark Stone Grey
14 x | 278026 CONNECTOR PEG W.
FRICTION - Black | 8 x | 4211815 CROSS AXLE 3M - Medium
Stone Grey | 5 x | 4227155 BUSH FOR CROSS AXLE -
Bright Red
12 x | 4189110

CONN.BUSH
W.FRIC./CROSSALE -
Bright Blue
2 x | 370526 CROSS AXLE 4M - Black | 16 x | 4514553 CONNECTOR PEG W. FRICTION 3M - Bright Blue
2 x | 4107085 ANGLE ELEMENT, 0
DEGREES [1] - Black | 4 x | 4515183 BEAM 1X2 W/CROSS AND
HOLE - Dark Stone Grey | 2 x | 4560177

CROSS AXLE 4M WITH
END STOP - Dark Stone
Grey
6 x | 4121667 DOUBLE CROSS BLOCK -
Black | 2 x | 370726 CROSS AXLE 8M - Black | 2 x | 4107783 ANGLE ELEMENT, 180 DEGREES [2] - Black
1 x | 373726 CROSS AXLE 10M - Black | 4 x | 4225033 BEAM 3 M. W/4 SNAPS -
Medium Stone Grey | 2 x | 4211450 TOOTHED BAR M=1, Z=10
- Medium Stone Grey

1 x | 3226901 DOUBLE CONICAL WHEEL
Z20 1M - White | 2 x | 4514558 GEAR WHEEL Z24 - Dark Stone Grey

© 2012 The LEGO Group. All rights reserved. Use of the LEGO Digital Designer html print tool, signifies your agreement to the terms of use.

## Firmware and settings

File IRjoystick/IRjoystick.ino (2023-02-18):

//Programma per la rilevazione e la trasmissione dei dati del Joystick (Shield v1.a Funduino) da usare come telecomando

#include <IRremote.h>             //Libreria per la trasmissione infrarossi
IRsend irsend;                    //Utilizzo della libreria in modalità di invio dei segnali, LED infrarossi collegato necessariamente al PIN=3

const byte PIN_X = 0;             //PIN per la coordinata orizzontale del joystick
const byte PIN_Y = 1;             //Coordinata verticale

//Calibrazione joystick: i valori corrispondono a quelli che il Joystick trasmette quando si trova in posizione
const float x_max = 983;          //orizzontale - tutto a destra
const float x_med = 492;          //orizzontale - centro
const float x_min = 0;            //orizzontale - tutto a sinistra
const float y_max = 1023;         //verticale - tutto giù
const float y_med = 499;          //verticale - centro
const float y_min = 0;            //verticale - tutto giù

long va,vb,pos;                   //Dati per il voltaggio dei morsetti del motore, posizione del servo motore (long per evitare errori di overflow durante i calcoli successivi)
long xread,yread;                 //Attuale posizione verticale (y) e orizzontale (x) del joystick
long hexIR;                       //Stringa esadecimale da inviare tramite infrarossi
 
void setup() {
}

void loop() {
  
  xread = analogRead(PIN_X);                      //Lettura dati attuali del joystick
  yread = analogRead(PIN_Y);

  va=15/(y_min-y_med)*(yread-y_med);              //Calcolo delle variabili per il controllo dei motori mediante funzioni lineari con parametri i dati di calibrazione
  vb=15/(y_max-y_med)*(yread-y_med);              //va=0 per yread=y_med, va=15 per yread=y_min; vb=0 per yread=y_med, vb=15 per yread=y_max 
  pos=16/(x_max-x_min)*(xread-x_min);             //pos=8 per xread=x_med, pos=0 per xread=x_min, pos=16 per xread=x_max (16 per avere il valore 8 come centrale)

  if(va<0) va=0;                                  //Correzzione valori non accettati dovuti alla struttura delle funzioni ed eventuali calibrazioni sbagliate
  if(va>15) va=15;                                //Necessaria per esser sicuri di avere ogni dato di massimo 4 bit
  if(vb<0) vb=0;
  if(vb>15) vb=15;
  if(pos<0) pos=0;
  if(pos>15) pos=15;                              //Inevitabilmente pos diventa asimmetrico (7 gradazioni per girare a destra, 8 a sinistra)

  /*A questo punto le varibili di controllo dei motori rispondono alla posizione del joystick come sotto 
   * (possono presentarsi anche valori intermedi tra quelli riportati)
   * 
   *       pos   va   vb     xread  yread     Posizione joystick                Movimento auto:
   *         8    0    0     x_med  y_med     Joystick rilasciato               Auto ferma, ruote dritte
   *         0    0    0     x_min  y_med     Joystick a tutto a sinistra       Auto ferma, ruote tutto a sinistra
   *        15    0    0     x_max  y_med     Joystick a tutto a destra         Auto ferma, ruote tutto a destra
   *         8   15    0     x_med  y_min     Joystick tutto giù                Auto all'indietro a massima velocità, ruote dritte
   *         8    0   15     x_med  y_max     Joystick tutto su                 Auto in avanti a massima velocità, ruote dritte
   */

  hexIR=pos*0x100+va*0x10+vb;                     //Creazione stringa esadecimale del tipo |pos|va|vb| (errori di overflow in caso di varibili di tipo int)

  for(int i=0; i<3; i++){ 
    irsend.sendSony(hexIR, 12);                   //Invio stringa esadecimale tramite infrarossi secondo lo standard Sony
    delay(100);
  }
}

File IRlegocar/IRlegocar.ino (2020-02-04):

/* © Lorenzo D'Auria
 *   Program for controlling a car by receiving an IR signal
*/

#include <IRremote.h>           //IR library
const int IR_PIN = 11;          //IR receiver PIN (11 in this case)
IRrecv irrecv(IR_PIN);          //Initialazing the IR sensor
decode_results results;

#include <Servo.h>              //Initializing servo motor
Servo ser;

#define a 6                     //DC motor PIN connect IN1 to PIN 6 and IN2 to PIN 5 of the H bridge
#define b 5
const int med=88;               //Servo motor calibration; Neutral postion
const int lf=35;                //Full left position
const int rg=135;               //Full right postion

long va=0;                      //DC motor alimentation
long vb=0;
long pos=med;                   //Servo motor position
unsigned long tric;             //Last reception time


void setup() {
  Serial.begin(9600);           //Only for debug or calibration
  pinMode(a,OUTPUT);            //DC motor PIN set up
  pinMode(b,OUTPUT);
  irrecv.enableIRIn();          //Start the IR reception
  irrecv.blink13(true);         //LED 13 blinks when receives data
  ser.attach(9);                //Servo motor PIN (9 in this case)
}


void loop() { 
  if (irrecv.decode(&results)) {                                     //IR sensor receives something
    if(results.decode_type==SONY && results.bits==12){               //Check of the received data
        tric=millis();                                               //Update last reception time
        pos=results.value/0x100;                                     //Calculation of the position of the servo motor
        va=(results.value-pos*0x100)/0x10;                           //Calculation of the speed of the DC motor
        vb=results.value-pos*0x100-va*0x10;
        if (pos>8) pos=(pos-8)*((rg-med)/7)+med;                     //Values adjustment due to servo calibration
        else pos=(pos-8)*((med-lf)/8)+med;
        va=va*17;                                                    //Values adjustment due to the transmission method
        vb=vb*17;
    }
    irrecv.resume();                                                 //IR sensor is ready to receive data again
  }
  
  if(millis()-tric>1000) {va=0; vb=0; pos=med;}                      //Out of signal check (signal is absent for more than 1 second)

  if(va*vb==0){                               //Security check of the calculated data, if correct
    analogWrite(a,va);                        //Control motor as received from the remote
    analogWrite(b,vb);
    ser.write(pos);
  }

  //Serial.println(results.value,HEX);        //Remove "//" to see what the IR sensor has received
  /*
  Serial.print(va);                           //Remove comment to see which values has been calculated
  Serial.print("   ");
  Serial.print(vb);
  Serial.print("   ");
  Serial.println(pos);
  */
}
